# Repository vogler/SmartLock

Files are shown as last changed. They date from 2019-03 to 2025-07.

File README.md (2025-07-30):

# DIY SmartLock
3D printed smart lock using ESP32 via 2 AA cells, N20 geared motor driven by TB6612FNG via 9V block.

Designed with Fusion 360. [Here](https://a360.co/4lLHHwa) you can view the model online and download it in various formats.
The STL files for 3d-printing the 4 parts are also available in [`stl`](https://github.com/vogler/SmartLock/tree/master/stl).
The slot for the key has some clearance. I wrapped some insulating tape around the end of the key to make a good fit.

The ESP32 goes into deep sleep and wakes up using the capacitive touch sensor on pin `T2` which is connected to the metal case around the lock. Since this is connected to the metal door knob on the outside of the door, it is enough to touch the door knob outside to wake up the ESP32 and open the door.
Whether it should open or not can be set via MQTT on `door/auth` which is checked via WiFi on wake.
This is pretty flexible with MQTT dashboard on the phone or some automation with presence detection in node-red on the RPi.


[Album](https://photos.app.goo.gl/bewiZ1qH8sHnJjmg7) with more photos and videos of the lock in action.

## Log
1. Test which motor is strong enough
    - geared motor at 9V can close lock and open door
      - at 5V from power bank only enough to close and open the lock but not enough to pull the [trap](https://de.wikipedia.org/wiki/Schlossfalle) open
      - at 4.7V from LiPo already can't close lock anymore
2. Design frame for door, key and motor
    - used Fusion 360: file, stl on thingiverse.com
3. 3D print
    - used Ultimaker 2 with black filament
      - Cura settings: file
    - everything worked on the first try, fit perfectly and seems strong enough - lucky?
4. How to control? -> ESP32 (board or bare)
    - ESP8266's deep sleep current is too high and only has WiFi.
    - ESP32's deep sleep current is very low (depending on the board) and it also has bluetooth.
4. How to power? -> 2 AA and 9V block
    - 2*AA batteries ~= 3.2V for ESP32: alkaline < 5 Wh
    - 9V block battery for motor: alkaline < 3 Wh
    - could also step-down from 9V or step-up from 3.2V
      - step-up from 3.2V seems better since ESP is running more often than the motor and AA have higher capacity
      - converter efficiency?
      - constant current drain if we do not cut it off?
5. Test motor control
    - first tried L293D: only works at 5V (only one direction worked at 3.2V)
    - then tried TB6612FNG Wemos I2C motor shield: works and specs are more than enough (two motors, 2.7-5.5V logic, <15V motor, 1.2A const./3.2A peak per channel)
      - also have just the chip without a STM32 for I2C - probably needs less power (but some more cables), however the overhead of the shield seems low enough when put in standby
6. How to open door? -> touch door knob
    - constantly check via bluetooth if phone is close, and pull open if within certain distance (RSSI good enough?)
      - seems unreliable and energy-intense - how long can the motor pull it open w/o damage?
    - trigger it manually from phone via bluetooth/WiFi -> don't want to take phone out
    - detect touch of door knob and open then
      - ESP32 can stay in deep sleep and wake up from touch via one of its touch pins; metal on the inside is connected to the outside of the door
      - authentification fast enough to do it only after waking up? -> yes
      - works fine when powered via USB, but difference of no-touch vs. touch is very small when running on batteries (lower voltage, less ground capacitance?)
        - tried to increase accuracy by increasing measurement time
        - seems a bit better with USB cable hanging
        - found some threshold that works (see comments), but have to test if reliable under changing temperature, voltage etc.
7. How to authenticate?
    - not at all: everyone can open the door if they know they just have to touch it (which no one would probably do :))
    - have some touch Morse code: takes too long
    - via bluetooth or phone connected to WiFi:
      - needs some logic that it only opens after some time away
        - what if I'm out running without my phone?
    - bluetooth
      - ESP32 as client: need some server running on the phone
      - ESP32 as server that phone connects to
        - auto-connect doesn't seem to work, don't want to manually connect
      - BLE scan for set of devices: not encrypted, can be spoofed
        - phone does not advertise, would have to start e.g. via nRF Connect; but maybe can be automated
        - watch only advertises if not connected to phone
        - bluetooth beacons advertise but need to be turned on first
        - Stryd footpod: advertises when not in use only?
    - WiFi: do presence detection on the RPi and ask it whether to open
      - phone connected to WiFi (already connects at the elevator)
      - yes if sequence: door sensor open/close, no motion, phone disconnected from WiFi for x min, phone connected to WiFi

## Links
- [Youtube: Comparison of 10 ESP32 Battery powered Boards without display (incl. deep-sleep)](https://www.youtube.com/watch?v=-769_YIeGmI)
    - [ESP32 Boards Comparison](https://docs.google.com/spreadsheets/d/1Mu-bNwpnkiNUiM7f2dx8-gPnIAFMibsC2hMlWhIHbPQ/edit#gid=0): LOLIN D32: 125 uA deep sleep from battery
- [ESP32 API: Touch Sensor](https://docs.espressif.com/projects/esp-idf/en/latest/esp32/api-reference/peripherals/touch_pad.html)
- [ESP32 Capacitive Sensors](https://nick.zoic.org/art/esp32-capacitive-sensors/): maybe the difference USB<>battery is because of the bigger ground plane with USB
- [Touch Sensor Application Note](https://github.com/espressif/esp-iot-solution/blob/e330b4d3ed947c7a99b448983096797e65be81c9/documents/touch_pad_solution/touch_sensor_design_en.md)

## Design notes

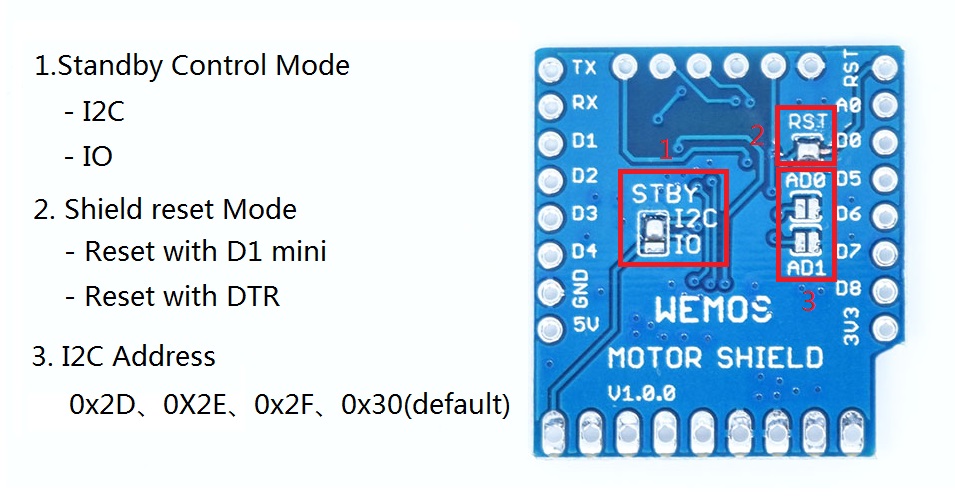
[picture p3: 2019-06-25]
datasheets/WeMosD1MiniMotorShield Modes.jpg

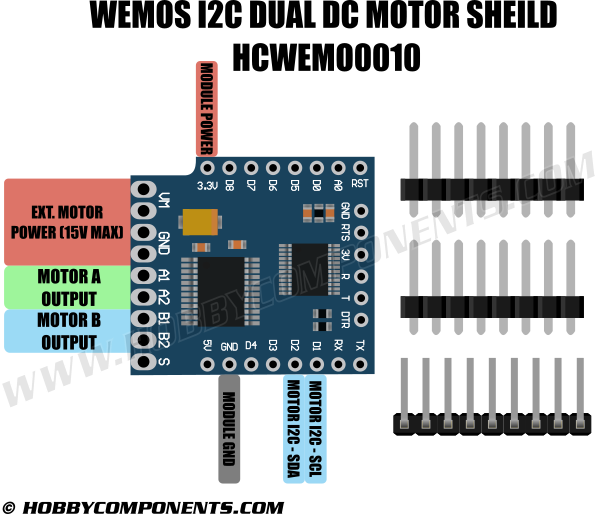
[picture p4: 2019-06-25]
datasheets/WeMosD1MiniMotorShield Connections.png

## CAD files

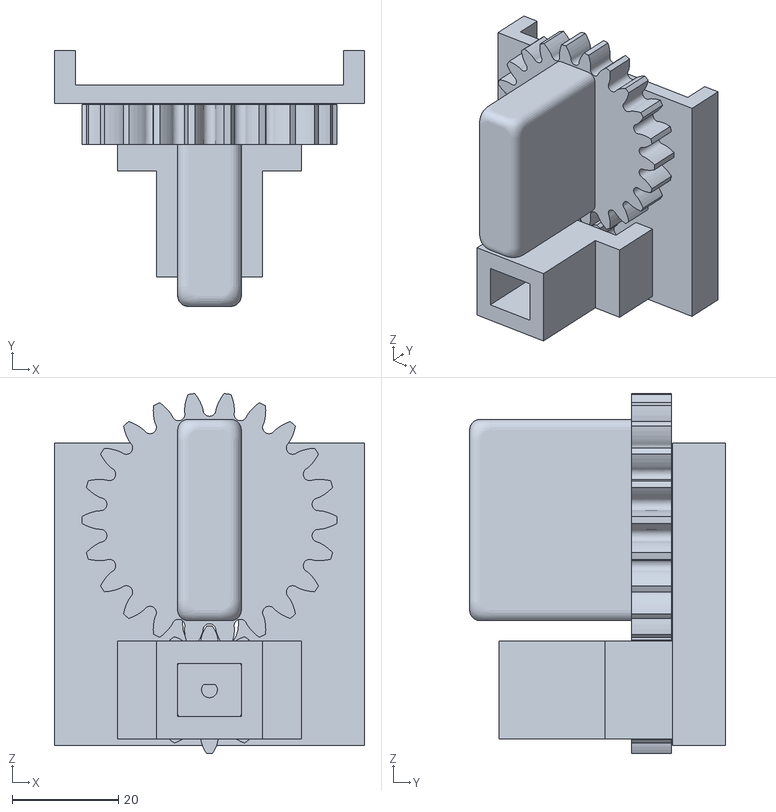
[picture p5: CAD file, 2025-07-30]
stl/0-SmartLock-assembled.stl
58.5 x 48.2 x 67.8

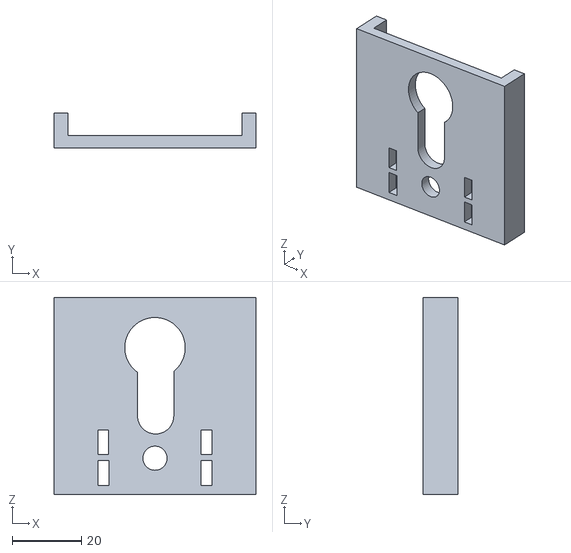
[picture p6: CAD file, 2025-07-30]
stl/1-base.stl
58.5 x 10.0 x 57.1

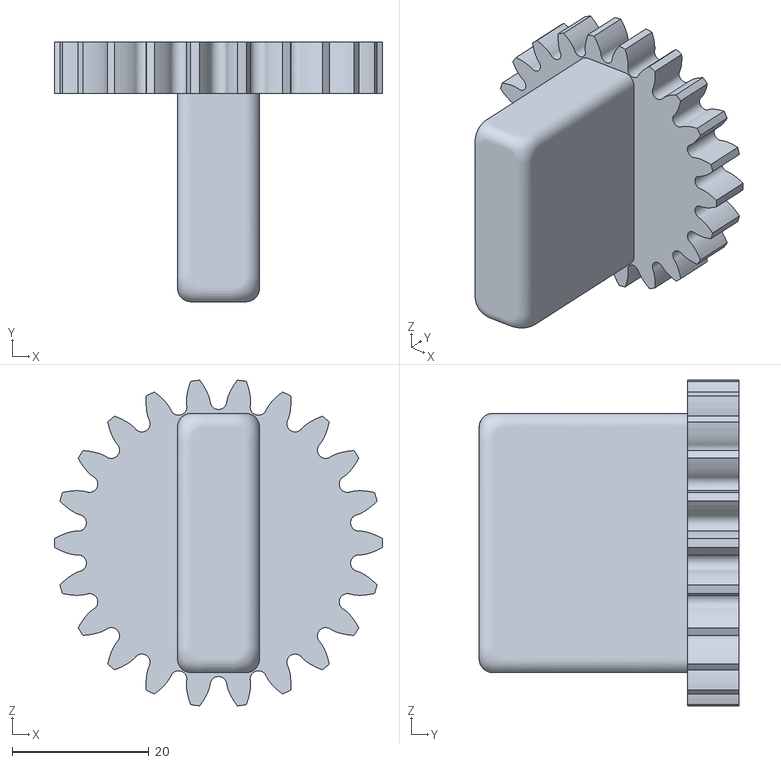
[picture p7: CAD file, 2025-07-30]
stl/4-gear-key-knob.stl
48.0 x 38.0 x 47.7

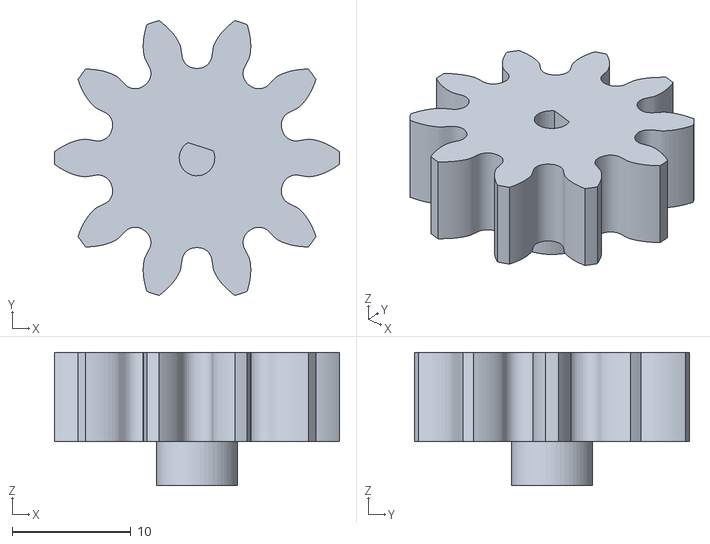
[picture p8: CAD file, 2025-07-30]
stl/2-gear-motor.stl
24.0 x 23.1 x 11.2

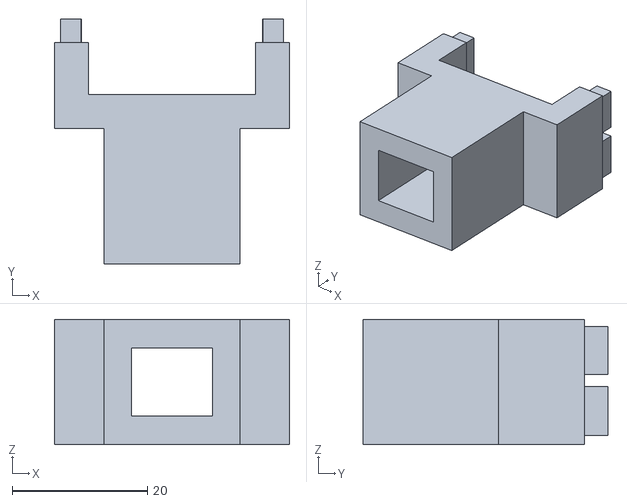
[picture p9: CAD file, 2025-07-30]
stl/3-cage-motor.stl
34.7 x 36.2 x 18.5

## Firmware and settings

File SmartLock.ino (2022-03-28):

// 3D printed smart lock using:
// - bare ESP32 (WROOM-32)
//   - power via 2 AA batteries
// - N20 geared motor driven by TB6612FNG (see lib/ and dev/ for I2C motor shield version)
//   - power via 9V block battery
// see README.md and folder dev for more details/examples

// power consumption (motor at 9 V, ESP32+shield at ~3.2 V of 2 AA)
//   motor: ~40 mA no load
//   DOIT DEVKIT V1: 48.2 mA, 10 mA deep sleep
//   LOLIN D32: 39.4 mA, 0.7 mA deep sleep
//   bare ESP32: 36.8 mA, 5.2 uA deep sleep, with shield connected 16.9 uA?
//   TB6612FNG I2C shield: 2.8 mA, 1.8 mA in standby?
//   TB6612FNG bare: ?


// #include "WEMOS_Motor.h"
// Motor M1(0x30, _MOTOR_B, 1000);
// changed from I2C shield to controlling TB6612FNG directly:
#define PIN_STBY 26
#define PIN_BIN1 27
#define PIN_BIN2 14
// PIN_PWM is pulled high directly since we do not need it

// see table in TB6612FNG.pdf on page 4
void motor(const byte in1, const byte in2, const byte stdby){
  digitalWrite(PIN_BIN1, in1);
  digitalWrite(PIN_BIN2, in2);
  digitalWrite(PIN_STBY, stdby);
}
void motor_brake(){ motor(HIGH, HIGH, HIGH); }
void motor_CCW(){   motor(LOW, HIGH, HIGH); }
void motor_CW(){    motor(HIGH, LOW, HIGH); }
void motor_stop(){  motor(LOW, LOW, HIGH); }
void motor_standby(){
  digitalWrite(PIN_STBY, LOW);
}


// Wake from deep sleep via capacitive touch sensor.
// Need to define some threshold, value lowers when touched. When connected via USB, the difference is quite high, but when running on batteries very low.
// on batteries with USB cable dangling: 99-103 no-touch vs. 92-96 touch
#define TOUCH_TH 98 // touch threshold, values usually 2-12 with finger depending on how hard the pinch, on batteries somehow higher
// with LOLIN D32 on USB at pin 15 usually ~60, pin held to screw on the inside: ~33, when touching knob from outside: ~21
// Fixed pin to metal frame on the inside. Via USB: no touch ~25, touch: 18-20, 22 as threshold works.
// However, from batteries, touchRead gives 34-37 with no difference whether touching the frame or not. 63-69 if pin is in the air. Only 39-43 if pinched directly.
// -> Somehow, on batteries my touching does not add any capacitance to that of the frame. Also touching the metal Macbook case does not make a difference on batteries, whereas the value even goes to 0 when running from USB.
bool touch1 = false;
bool touch2 = false;
void ICACHE_RAM_ATTR touch1_ISR(){ touch1 = true; }
void ICACHE_RAM_ATTR touch2_ISR(){ touch2 = true; }

#define SLEEP_TIMEOUT 5000 // go to deep sleep after 5s of no action


#include <MyConfig.h> // credentials, servers, ports

#include "WiFi.h"
WiFiClient wifi;

#define MQTT_TOPIC_AUTH "door/auth"
bool auth = false;
#define MQTT_TOPIC_LOG  "door/log"
// json
char buf[200];
#define json(s, ...) (sprintf(buf, "{ " s " }", __VA_ARGS__), buf)
#define b2s(x) (x ? "true" : "false")

void mqtt_callback(char* topic, byte* payload, unsigned int length) {
  Serial.printf("MQTT message on topic %s with payload ", topic);
  for(int i = 0; i < length; i++){
    Serial.print((char) *(payload+i));
  }
  Serial.println();
  auth = *payload == '1';
}

#include <PubSubClient.h>
PubSubClient mqtt(MQTT_SERVER, MQTT_PORT, mqtt_callback, wifi);

void setup_wifi() {
  delay(5);
  Serial.printf("Connecting to AP %s", WIFI_SSID);
  const unsigned long start_time = millis();
  WiFi.mode(WIFI_STA);
  WiFi.begin(WIFI_SSID, WIFI_PASS);
  for (int i = 0; WiFi.waitForConnectResult() != WL_CONNECTED && i < 20; i++) {
    WiFi.begin(WIFI_SSID, WIFI_PASS); // for ESP32 also had to be moved inside the loop, otherwise only worked on every second boot, https://github.com/espressif/arduino-esp32/issues/2501#issuecomment-548484502
    delay(100);
    Serial.print(".");
  }
  const float connect_time = (millis() - start_time) / 1000.;
  Serial.println();
  if (WiFi.waitForConnectResult() != WL_CONNECTED) {
    Serial.printf("Failed to connect to Wifi in %.3f seconds. Going to restart!", connect_time);
    ESP.restart();
  }
  Serial.printf("Connected in %.3f seconds. IP address: ", connect_time);
  Serial.println(WiFi.localIP());
}

void setup_mqtt() {
  mqtt.setCallback(mqtt_callback);
  randomSeed(micros());
  while (!mqtt.connected()) {
    Serial.print("Attempting MQTT connection... ");
    String clientId = "SmartLock-ESP32-" + String(random(0xffff), HEX);
    if (mqtt.connect(clientId.c_str())) {
      Serial.printf("connected as %s to mqtt://%s\n", clientId.c_str(), MQTT_SERVER);
      while(!mqtt.subscribe(MQTT_TOPIC_AUTH)) Serial.print(".");
      Serial.printf("subscribed to topic %s\n", MQTT_TOPIC_AUTH);
    } else {
      Serial.printf("failed, rc=%d. retry in 1s.\n", mqtt.state());
      delay(1000);
    }
  }
}


void setup()
{
  Serial.begin(115200);
  Serial.println("setup");

  // TB6612FNG motor driver pins
  pinMode(PIN_BIN1, OUTPUT);
  pinMode(PIN_BIN2, OUTPUT);
  pinMode(PIN_STBY, OUTPUT);

  // use touch interrupts instead of touchRead in loop because it sometimes triggers without touch (maybe if reading too often?)
  touchAttachInterrupt(T2, touch1_ISR, TOUCH_TH);
  // touchAttachInterrupt(T3, touch2_ISR, TOUCH_TH);

  // read the current touch voltage settings
  touch_high_volt_t refh; touch_low_volt_t refl; touch_volt_atten_t atten;
  touch_pad_get_voltage(&refh, &refl, &atten);
  Serial.printf("touch_pad_get_voltage: refh: %d, refl: %d, atten: %d\n", refh, refl, atten);
  // refh: 3, refl: 0, atten: 3
  // refh: TOUCH_HVOLT_2V7, refl: TOUCH_LVOLT_0V5, atten: TOUCH_HVOLT_ATTEN_0V
  // touch_pad_set_voltage(TOUCH_HVOLT_2V4, TOUCH_LVOLT_0V8, TOUCH_HVOLT_ATTEN_0V); // batteries: 160, 150-157

  // increase touch accuracy by increasing measurment time; otherwise touch does not make enough difference when running on batteries (via USB it is ok)
  touchSetCycles(0x3000, 0x1000); // cycles for measure & sleep, default for both is 0x1000 which results in touchRead taking 0.5ms
  // no-touch, touch on batteries:
  // 0x3000, 0x1000: 118, 108-114
  // 0x6000, 0x2000: 231-236, 223-227
  // 0x6000, 0x6000: 231-236, 226-231

  esp_sleep_enable_touchpad_wakeup();

  setup_wifi();
  setup_mqtt();
  mqtt.publish(MQTT_TOPIC_LOG, json("\"millis\": %lu, \"action\": \"wakeup\"", millis())); // takes ~500-700ms
}

void deep_sleep() {
  // BT and WiFi off; not sure if needed...
  btStop();
  // WiFi.mode(WIFI_OFF);
  WiFi.disconnect(true); // true = WiFi off
  esp_deep_sleep_start();
}

unsigned long last_action;

void loop()
{
  mqtt.loop();
  // overview which pins are save to use: https://randomnerdtutorials.com/esp32-pinout-reference-gpios/
  // pins falling below threshold without touching: 32, 33
  // const byte touch_open  = touchRead(2);
  // const byte touch_close = touchRead(15); // if the first read drops below threshold, the second one will go to 0 as well after some time
  // sadly all touch pins report 0 every ~20 iterations without being touched, so we have to ignore 0
  // without touch the values are ~60-80, with touch 1-15
  // bool do_open  = touch_open && touch_open < TOUCH_TH;
  // bool do_close = touch_close && touch_close < TOUCH_TH;
  // if (do_open || do_close)
    // Serial.printf("touch: open %d, close %d\n", touch_open, touch_close);

  delay(100);
  if(touch1) Serial.println("Touch 1 detected");
  if(touch2) Serial.println("Touch 2 detected");
  uint16_t touch1a = touchRead(T2);
  Serial.printf("touch1 %d\n", touch1a);
  bool do_open = touch1;
  bool do_close = touch2;
  touch1 = false; touch2 = false;

  // for finding the right touch threshold: report value and comment out sleep since we would not wake up
  // mqtt.publish(MQTT_TOPIC_LOG, json("\"millis\": %lu, \"action\": \"%s\", \"touch\": %d, \"auth\": %s", millis(), do_open ? (do_close ? "both" : "open") : "close", touch1a, b2s(auth)));

  if (do_open || do_close) {
    last_action = millis();
    mqtt.publish(MQTT_TOPIC_LOG, json("\"millis\": %lu, \"action\": \"%s\", \"touch\": %d, \"auth\": %s", millis(), do_open ? (do_close ? "both" : "open") : "close", touch1a, b2s(auth)));
  } else if (millis() - last_action > SLEEP_TIMEOUT) {
    Serial.printf("Going to sleep because there was no action for %d ms\n", SLEEP_TIMEOUT);
    // mqtt.publish(MQTT_TOPIC_LOG, json("\"millis\": %lu, \"action\": \"sleep\"", millis())); // does not get sent (probably needs delay before turning off)
    deep_sleep();
  }

  if (do_open && do_close) {
    motor_standby();
    esp_sleep_enable_timer_wakeup(20 * 1000 * 1000);
    Serial.println("Going to sleep for 20s because you told me to.");
    deep_sleep();
  }
  else if (auth && do_open) motor_CCW();
  else if (auth && do_close) motor_CW();
  else motor_standby();
}

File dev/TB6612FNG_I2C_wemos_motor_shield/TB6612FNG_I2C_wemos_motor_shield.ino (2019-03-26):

// WEMOS I2C Dual Motor Shield (TB6612FNG)
// https://hobbycomponents.com/shields/869-wemos-d1-mini-motor-drive-shield
// Connected D1 to GPIO22, D2 to GPIO21. Wasn’t detected by i2c_scanner.
// Flashed fixed firmware according to
// https://hackaday.io/project/18439-motor-shield-reprogramming
// Afterwards detected at I2C address 0x30, but motor doesn’t move with any sketch.
// Found out that Standby pin of the IC must be pulled high, but it's not connected to anything.
// There are solder pads on the back for I2C and IO (control via extra pin S).
// Docs said I2C is the default, but apparently not for this clone.
// After soldering bridge STBY I2C, it worked.

#include "WEMOS_Motor.h"

Motor M1(0x30, _MOTOR_B, 1000);

void setup()
{
  Serial.begin(250000);
  Serial.println("setup");
}

float pwm;
void loop()
{
  Serial.printf("\r\nTest PWM 30 to 100, step 0.5,CW\r\n");
  for (pwm = 30; pwm <= 100; pwm += 0.5)
  {
    M1.setmotor( _CW, pwm);
    Serial.println(pwm);
  }

  M1.setmotor(_STOP);

  Serial.println("Motor B STOP");
  delay(200);

  Serial.printf("Test PWM 30 to 100, step 0.5,CCW\r\n");
  for (pwm = 30; pwm <= 100; pwm += 0.5)
  {
    M1.setmotor(_CCW, pwm);
    Serial.println(pwm);
  }

  M1.setmotor(_STOP);

  Serial.println("Motor B STOP");
  delay(200);
  M1.setmotor(_CW, 50); delay(500);

//  esp_sleep_enable_timer_wakeup(5000 * 1000);
//  esp_deep_sleep_start();
}

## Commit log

2019-03-26 control N20 geared motor with L293D on ESP32
2019-03-26 power consumption of DOIT board and bare ESP32 on 2 AA batteries
2019-03-26 Arduino concats all .ino files in the sketch folder on build...
2019-03-26 WEMOS I2C Dual Motor Shield (TB6612FNG) can deal with 3.3V
2019-03-26 control motor with touch via cables, using DOIT board
2019-04-01 notes on power consumption, played around with touch threshold
2019-06-25 add data sheets for motor driver, STM32 on I2C shield, and some board pinouts
2020-01-27 add examples, WEMOS_Motor_Shield in lib/ as submodule, forceInclude arduino and pins
2020-01-27 move each .ino into its own folder to be able to flash it...
    vscode-arduino then asks which sketch to flash; also works in the Arduino IDE.
    Tried platformio, but it does not allow to have several main files inside a project.
    Would need to duplicate platformio.ini and have several folders in a workspace.
    Also, the only dependency I have is not available in the official repository anyway.
2020-01-28 switch from TB6612FNG I2C shield to bare chip, no more need for lib & less power?
2020-01-29 links to ESP32 comparison
2020-01-29 touch sensor links
2025-07-30 add stl files for 3d printing the 4 parts, closes #1
    [0-SmartLock-assembled.stl, 1-base.stl, 2-gear-motor.stl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]
